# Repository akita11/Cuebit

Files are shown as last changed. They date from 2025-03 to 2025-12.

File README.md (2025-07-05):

# Cue:bit

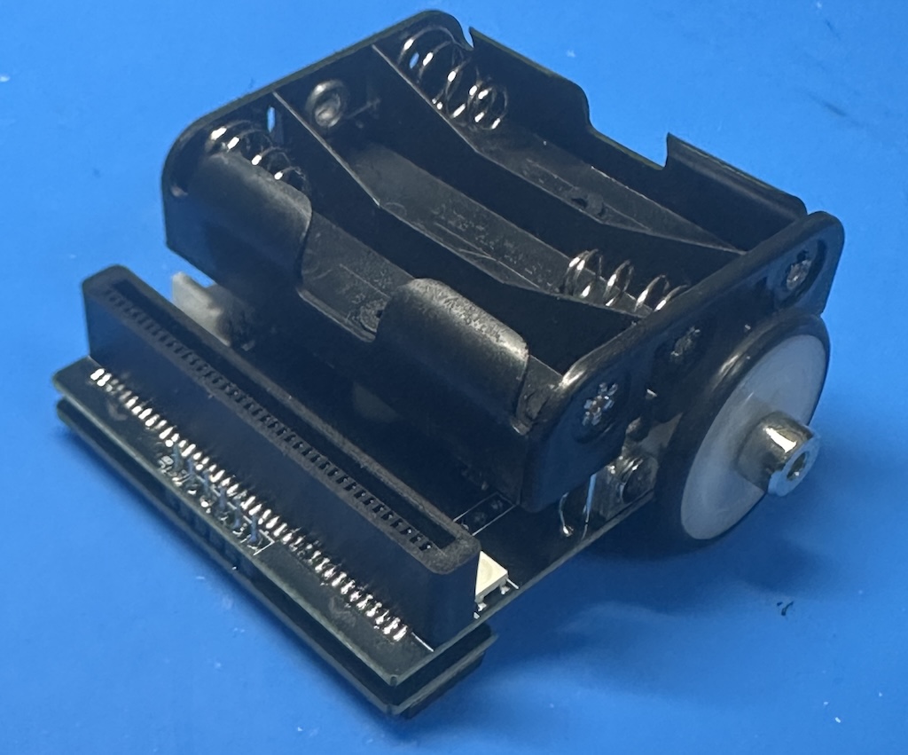
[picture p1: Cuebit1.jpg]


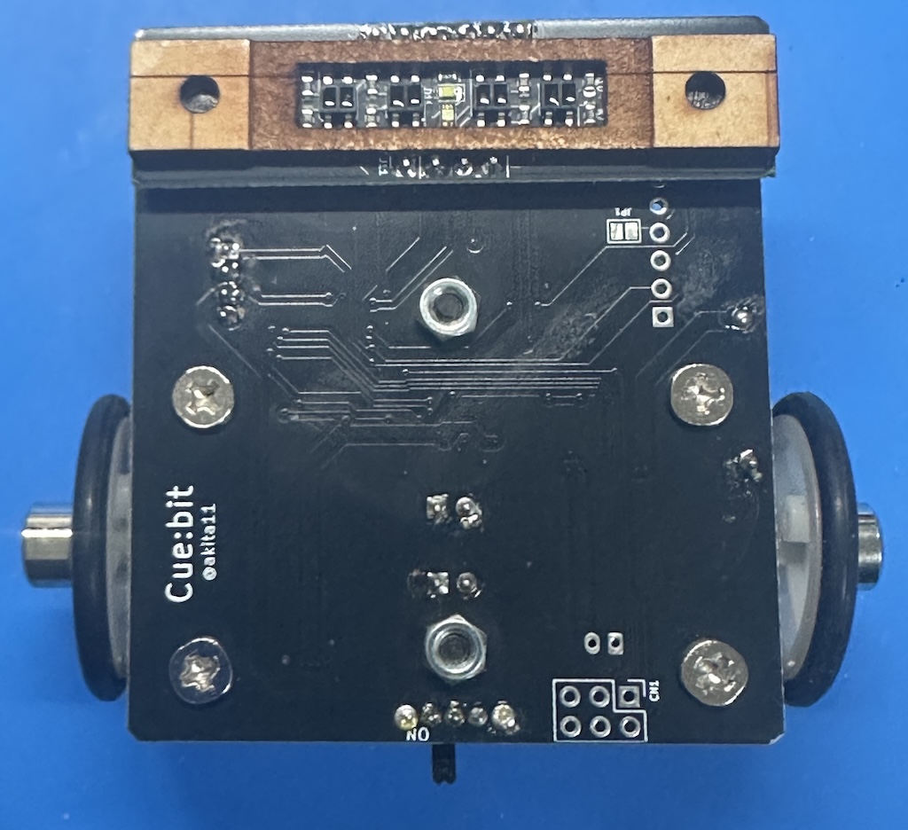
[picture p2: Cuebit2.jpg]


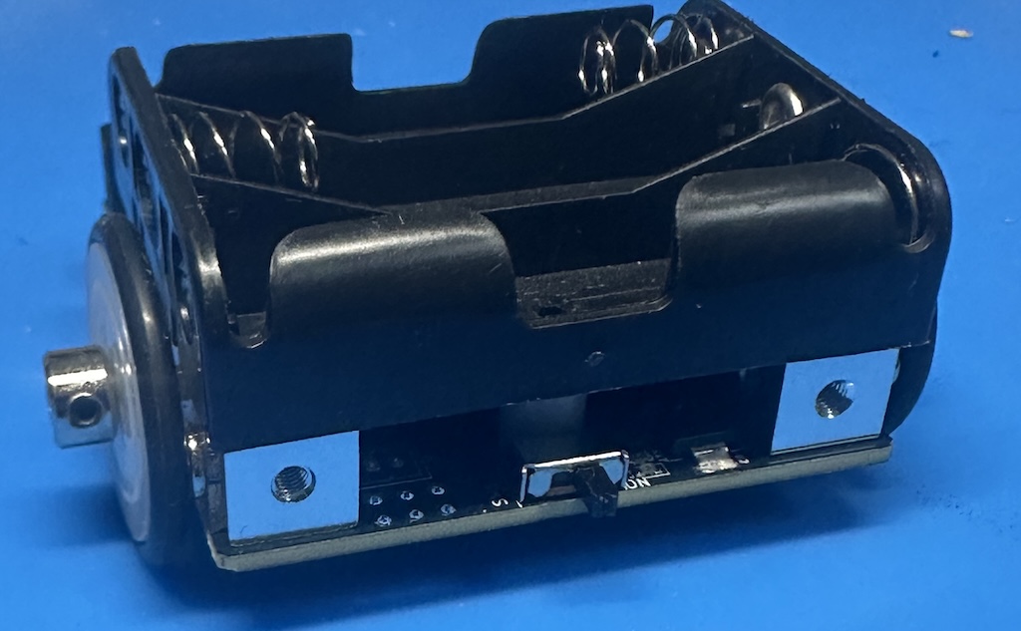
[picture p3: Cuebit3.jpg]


ライントレースと3色のカラーマーカでの動作制御ができるプログラミング教材ロボットカーです。micro:bitを装着して、micro:bitのカスタムブロックで動作制御することもできます。

[使い方・動作の例(YouTube動画)](https://youtu.be/czKjS_mCOlM)

## 使い方（ライントレースモード）

電源を入れると、ライントレースを開始します。また途中にカラーマーカーがあると、それに応じた動作をします。なおライン（黒）やカラーマーカを見失って0,5秒程度経過すると、自動的に停止します（本体LEDが黄色点灯）。ラインやマーカのあるところに移動させると、動作を再開します。

### カラーマーカーと動作の定義

赤・緑・黄の3色のマーカを3つ連続して配置されたところを通過すると、その色パターンに応じた動作を行います。色マーカは10mm程度の「丸ポチシール」（DAISOなどで売っているもの）や、同等の色を印刷したものを使います。(赤=R／緑=G／黄=Y）

- 緑-赤-黄 (GRY) : 速度を超ゆっくりに
- 赤-緑-黄 (RGY) : 速度をゆっくりに
- 赤-緑-赤 (RGR) : 速度を通常に
- 黄-緑-赤 (YGR) : 速度を速く
- 黄-赤-緑 (YRG) : 速度を超速く
- 黄-赤-黄 (YRY) : 一時停止（3秒程度）
- 緑-黄-赤 (GYR) : 次の交差点を左に90度曲がる
- 黄-緑-黄 (YGY) : 次の交差点を直進する
- 緑-黄-緑 (GYG) : 次の交差点を右に90度曲がる
- 赤-黄-赤 (RYR) : Uターンする
- 緑-赤-緑 (GRG) : バックする

## 使い方（micro:bitモード）

micro:bitのカスタムブロックを使ってCue:bitの動作を制御でききます。
[こちらの手順](https://docs.google.com/document/d/1bRiQpdVX2RdSoQZLEZQx14lWcuVc2Sd8CT0sPL3RYwU/)でMakeCode用カスタムブロックを追加し、micro:bitのプログラムを作成してmicro:bitに書き込みます。その後、そのmicro:bitをCue:bitに差し込んでCue:bitの電源をいれると、そのプログラム通りにCue:bitが動作します。

※モータの特性仕様上、左右の回転速度には差があり、以下のコマンドである程度は調整はできますが、完全に直進したり正確に指定距離だけ進む・回転することはできません。ご了承ください。

### 参考：技術的仕様

micro:bitからCue:bitへのコマンド（通信プロトコル:UART 9600bps N81）は以下です。以下の"NNN"は数値(10進数)で与えるコマンドパラメータです。また各コマンドは行末コード(0x0d or 0x0a)で終端します。なおCue:bitのGroveコネクタと本体後部の6ピンコネクタ用端子(FTDI-Basic用)も、micro:bitの通信端子と並列に接続されています。なお[「Groveケーブル-USBシリアル接続ケーブル」](https://www.switch-science.com/products/9460)を使うと、FTDI-Basicと本体Grove端子とを接続できます。なおソースコードはArduinoIDE等で書き込むことができます。（ターゲットはProMini(ATmega328P, 3.3V/8MHz)。新品ATmega328Pではこれ用のブートローダを書き込む必要あり）

- $ : micro:bit制御モードに開始
- \# : micro:bit制御モードを終了
- RNNN : NNN度回転（NNNが正=時計回り、負=反時計回り）（※実際の回転角度はモータ特性のばらつきなどから多少の誤差があります）
- B : 停止
- FNNN : NNN[cm]進む（※実際の移動距離はモータ特性のばらつきなどから多少の誤差があります）
- ZNNN : ジグザグ走行（およそNNN[cm]）
- SNNN : スケート走行（およそNNN[cm]）

以下はデバッグ用のコマンド

- P : パラメータの表示
- T : ライントレースモードを開始
- t : ライントレースモードを終了して停止
- D : デバッグ情報の表示を開始（Dに続けてr/g/y/wを書くと、色センサの値を各色の学習用のCSV形式で出力）
- d : デバッグ表示の表示を停止
- kNNN : ライントレース制御のKpパラメータ（float型）
- KNNN : ライントレース制御のKdパラメータ（float型）
- vNNN : 通常走行時の速度（float型。モータ駆動のPWM比として与えるため、値の範囲は0.0〜1.0）
- rNNN : 左右モータの速度調整（PWMデューティー比）（float型）（左モータのPWM比×r=右モータのPWM比として計算するため、v×rが1.0以下となること）
- fNNN : 1cm進むための時間[単位は10ms]（※実際の移動距離はモータ特性のばらつきなどから多少の誤差があります）
- gNNN : 10度回転するための時間[単位は10ms]（※実際の回転角度はモータ特性のばらつきなどから多少の誤差があります）
- ! : 各種パラメータをEEPROMに保存（起動時に読み込まれる）

## Author

Junichi Akita (@akita11) / akita@ifdl.jp

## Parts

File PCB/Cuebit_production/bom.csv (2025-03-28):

Designator | Footprint | Quantity | Value | LCSC Part #
C1, C2, C4, C5, C7 | C_0603_1608Metric | 5 | 0.1u | C14663
C3 | C_0603_1608Metric | 1 | 10u | C109454
D1 | LED_0603_1608Metric | 2 | LED(W) | C7371902
D2 |  |  | LED(G) | C165982
D3, D7 | LED_WS2812B_PLCC4_5.0x5.0mm_P3.2mm | 2 | WS2812B | C22461793
Q1 | SOT-23 | 1 | TR_NMOS_IRLML6344 | C20917
R10, R11, R15, R16, R5 | R_0603_1608Metric | 5 | 10k | C25804
R12, R13, R14, R7, R9 | R_0603_1608Metric | 5 | 470 | C2907172
R17 | R_0603_1608Metric | 1 | 1k | C21190
R18 | R_0603_1608Metric | 1 | 100 | C103204
R6, R8 | R_0603_1608Metric | 2 | 4.7k | C103656
U1 | TQFP-32_7x7mm_P0.8mm | 1 | ATmega328P-A | C14877
U2 | SOT-223-3_TabPin2 | 1 | AP1117-33 | C2763399
U3, U4 | SOT-23-6_L2.9-W1.6-P0.95-LS2.8-BL | 2 | AD116 | C2845121
U5, U6, U8, U9 | Everlight_ITR1201SR10AR | 4 | ITR8307-S17-TR8 | C81632
U7 | OPLGA-4 | 1 | SENSOR_VEML6040 | C78465
R1 | R_0603_1608Metric | 1 | 200k | C2907122
R2 | R_0603_1608Metric | 1 | 300k | C23024

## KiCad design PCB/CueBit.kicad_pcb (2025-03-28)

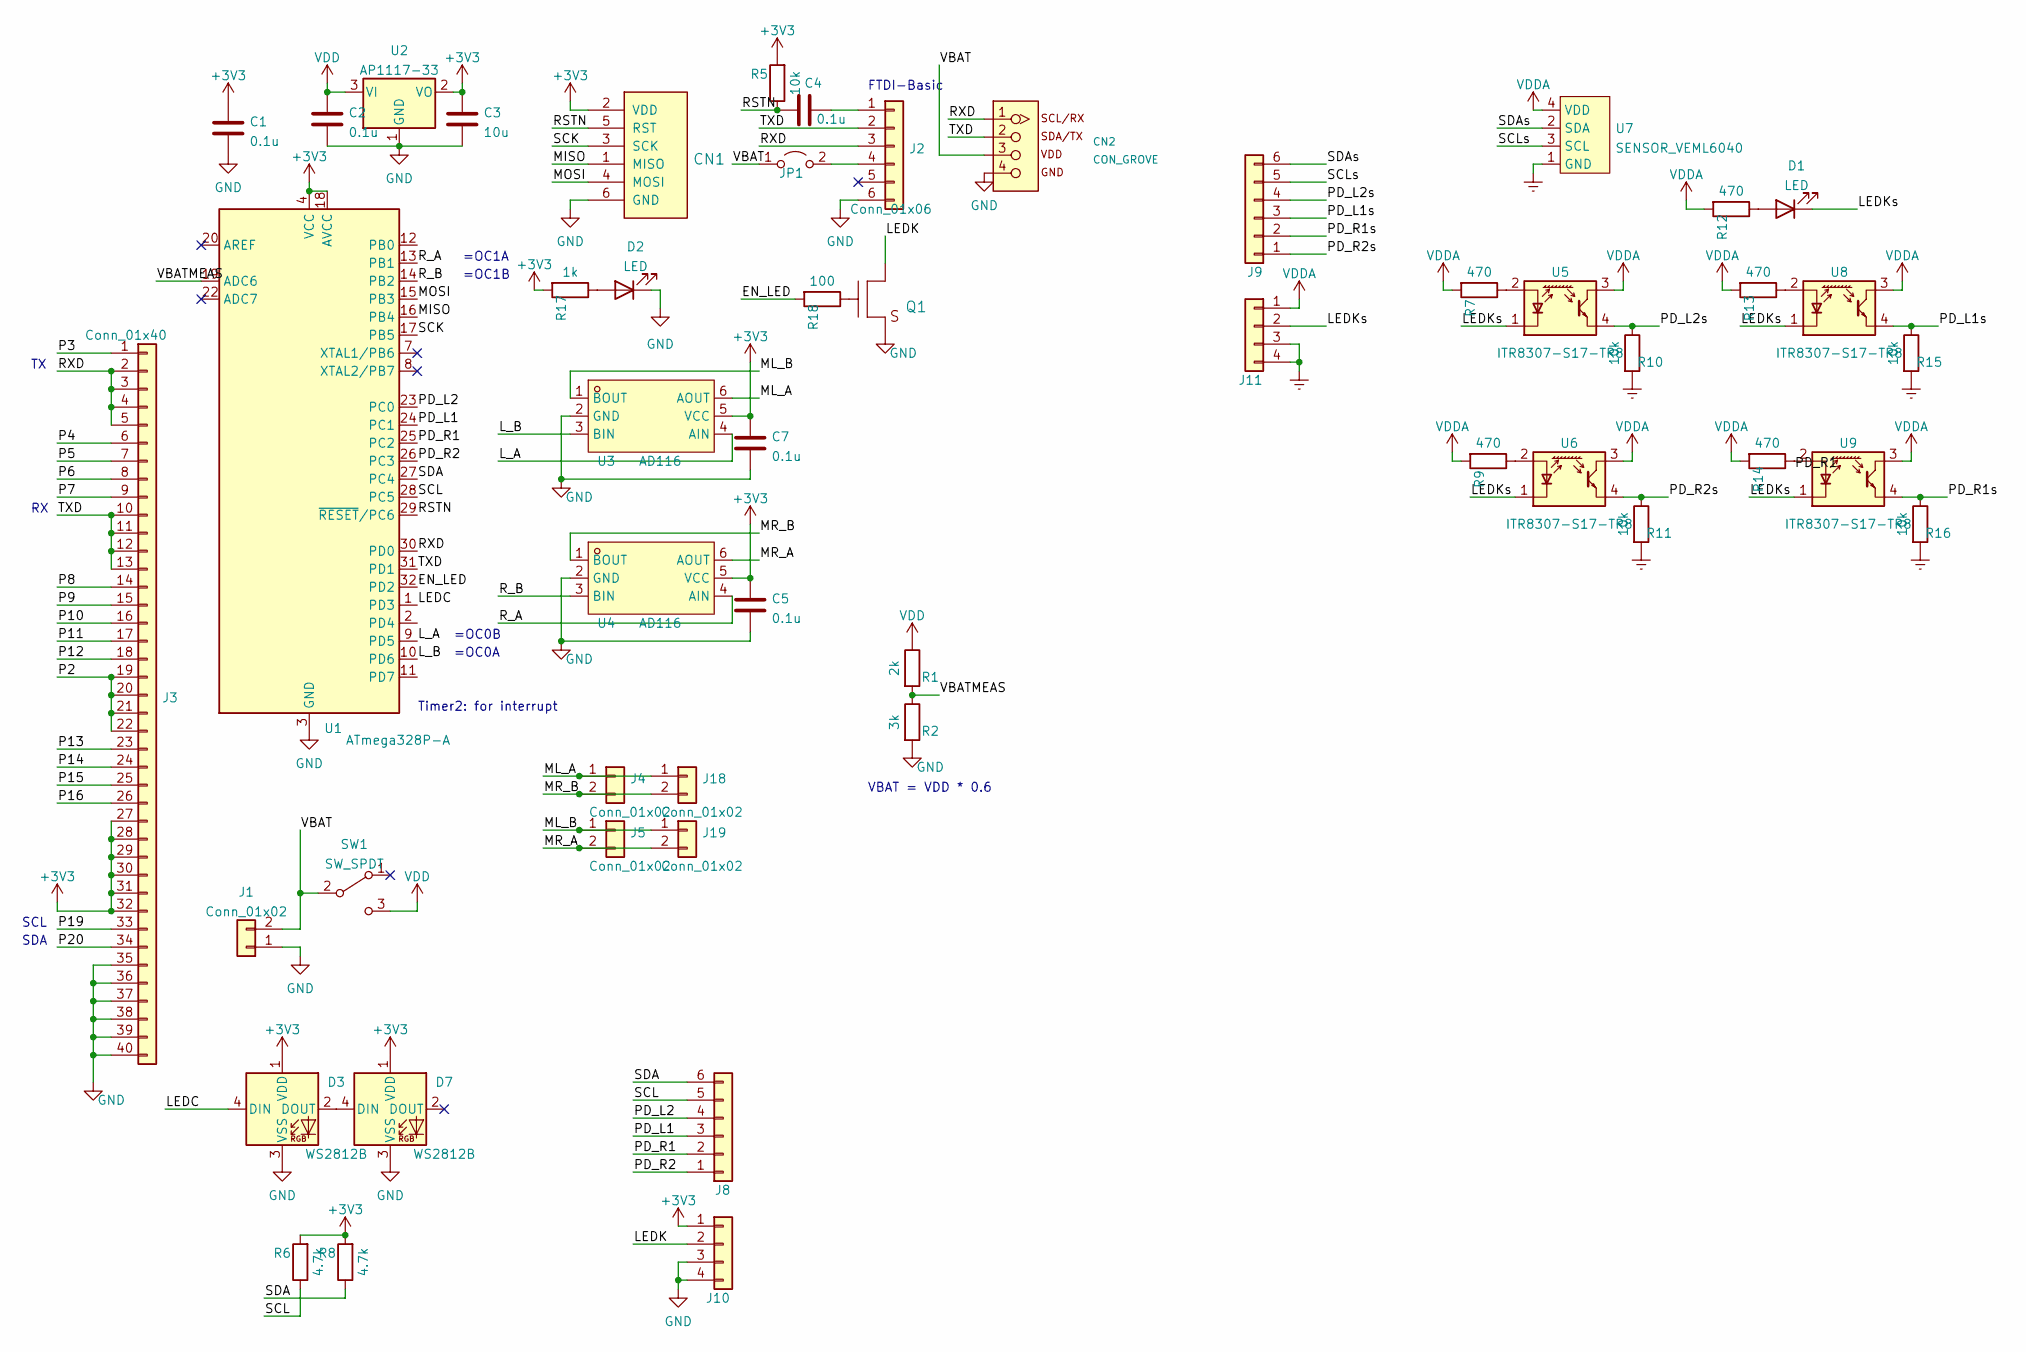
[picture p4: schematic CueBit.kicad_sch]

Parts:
C1, C2, C4, C5, C7: 0.1u; C_0603_1608Metric
C3: 10u; C_0603_1608Metric
CN1: CON_AVRISP; PinHeader_2x03_P2.54mm_Vertical
CN2: CON_GROVE; CON_GROVE_H_roundPad
D1, D2: LED; LED_0603_1608Metric
D3, D7: WS2812B; LED_WS2812B_PLCC4_5.0x5.0mm_P3.2mm
J1: Conn_01x02; JST_PH_B2B-PH-K_1x02_P2.00mm_Vertical
J2: Conn_01x06; PinSocket_1x06_P2.54mm_Vertical
J3: Conn_01x40; CON_microbit_cardedge_V_SMD
J4, J5: Conn_01x02; PinHeader_1x02_P2.54mm_Vertical
J8, J9: Conn_01x06; PinHeader_1x06_P2.54mm_Vertical
J10, J11: Conn_01x04; PinSocket_1x04_P2.54mm_Vertical
J18, J19: Conn_01x02; PinHeader_1x02_P2.54mm_Vertical_SMD_Pin1Right
JP1: Jumper_2_Open; SolderJumper-2_P1.3mm_Open_Pad1.0x1.5mm
Q1: TR_NMOS_IRLML6344; SOT-23
R1: 2k; R_0603_1608Metric; LCSC C2907022
R2: 3k; R_0603_1608Metric; LCSC C328357
R5, R10, R11, R15, R16: 10k; R_0603_1608Metric
R6, R8: 4.7k; R_0603_1608Metric
R7, R9, R12, R13, R14: 470; R_0603_1608Metric; LCSC C2907172
R17: 1k; R_0603_1608Metric
R18: 100; R_0603_1608Metric
SW1: SW_SPDT; SW_SK-12D11VG3
U1: ATmega328P-A; TQFP-32_7x7mm_P0.8mm; LCSC C14877
U2: AP1117-33; SOT-223-3_TabPin2; LCSC C2992570
U3, U4: AD116; SOT-23-6_L2.9-W1.6-P0.95-LS2.8-BL; LCSC Part C7463412
U5, U6, U8, U9: ITR8307-S17-TR8; Everlight_ITR1201SR10AR; LCSC C81632
U7: SENSOR_VEML6040; OPLGA-4; LCSC C78465

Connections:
+3V3: C1.1, C3.1, C5.1, C7.1, CN1.2 (VDD), D3.1 (VDD), D7.1 (VDD), J3.27, J3.28, J3.29, J3.30, J3.31, J3.32, J10.1, R5.2, R6.2, R8.2, R17.2, U1.4 (VCC), U1.6 (VCC), U1.18 (AVCC), U2.2 (VO), U3.5 (VCC), U4.5 (VCC)
/EN_LED: R18.2, U1.32 (PD2)
/LEDC: D3.4 (DIN), U1.1 (PD3)
/LEDK: J10.2, Q1.3 (D)
/LEDKs: D1.1 (K), J11.2, U5.1 (K), U6.1 (K), U8.1 (K), U9.1 (K)
/L_A: U1.9 (PD5), U3.4 (AIN)
/L_B: U1.10 (PD6), U3.3 (BIN)
/MISO: CN1.1 (MISO), U1.16 (PB4)
/ML_A: J4.1, J18.1, U3.6 (AOUT)
/ML_B: J5.1, J19.1, U3.1 (BOUT)
/MOSI: CN1.4 (MOSI), U1.15 (PB3)
/MR_A: J5.2, J19.2, U4.6 (AOUT)
/MR_B: J4.2, J18.2, U4.1 (BOUT)
/P2: J3.19, J3.20, J3.21, J3.22
/P3: J3.1
/P4: J3.6
/P5: J3.7
/P6: J3.8
/P7: J3.9
/P8: J3.14
/P9: J3.15
/P10: J3.16
/P11: J3.17
/P12: J3.18
/P13: J3.23
/P14: J3.24
/P15: J3.25
/P16: J3.26
/P19: J3.33
/P20: J3.34
/PD_L1: J8.3, U1.24 (PC1)
/PD_L1s: J9.3, R15.1, U8.4
/PD_L2: J8.4, U1.23 (PC0)
/PD_L2s: J9.4, R10.1, U5.4
/PD_R1: J8.2, U1.25 (PC2)
/PD_R1s: J9.2, R16.1, U9.4
/PD_R2: J8.1, U1.26 (PC3)
/PD_R2s: J9.1, R11.1, U6.4
/RSTN: C4.1, CN1.5 (RST), R5.1, U1.29 (~RESET/PC6)
/RXD: CN2.1, J2.3, J3.2, J3.3, J3.4, J3.5, U1.30 (PD0)
/R_A: U1.13 (PB1), U4.4 (AIN)
/R_B: U1.14 (PB2), U4.3 (BIN)
/SCK: CN1.3 (SCK), U1.17 (PB5)
/SCL: J8.5, R6.1, U1.28 (PC5)
/SCLs: J9.5, U7.3 (SCL)
/SDA: J8.6, R8.1, U1.27 (PC4)
/SDAs: J9.6, U7.2 (SDA)
/TXD: CN2.2, J2.2, J3.10, J3.11, J3.12, J3.13, U1.31 (PD1)
/VBAT: CN2.3, J1.2, JP1.1 (A), SW1.2 (B)
/VBATMEAS: R1.2, R2.1, U1.19 (ADC6)
Earth: J11.3, J11.4, R10.2, R11.2, R15.2, R16.2, U7.1 (GND)
GND: C1.2, C2.2, C3.2, C5.2, C7.2, CN1.6 (GND), CN2.4, D2.1 (K), D3.3 (VSS), D7.3 (VSS), J1.1, J2.6, J3.35, J3.36, J3.37, J3.38, J3.39, J3.40, J10.3, J10.4, Q1.2 (S), R2.2, U1.3 (GND), U1.5 (GND), U1.21 (GND), U2.1 (GND), U3.2 (GND), U4.2 (GND)
unnamed: C4.2, J2.1
unnamed: D1.2 (A), R12.1
unnamed: D2.2 (A), R17.1
unnamed: D3.2 (DOUT), D7.4 (DIN)
unnamed: J2.4, JP1.2 (B)
unnamed: Q1.1 (G), R18.1
unnamed: R7.1, U5.2 (A)
unnamed: R9.1, U6.2 (A)
unnamed: R13.1, U8.2 (A)
unnamed: R14.1, U9.2 (A)
VDD: C2.1, R1.1, SW1.3 (C), U2.3 (VI)
VDDA: J11.1, R7.2, R9.2, R12.2, R13.2, R14.2, U5.3, U6.3, U7.4 (VDD), U8.3, U9.3

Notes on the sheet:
SDA
VBAT = VDD * 0.6
Timer2: for interrupt
FTDI-Basic
=OC1A
=OC1B
=OC0B
=OC0A
SCL

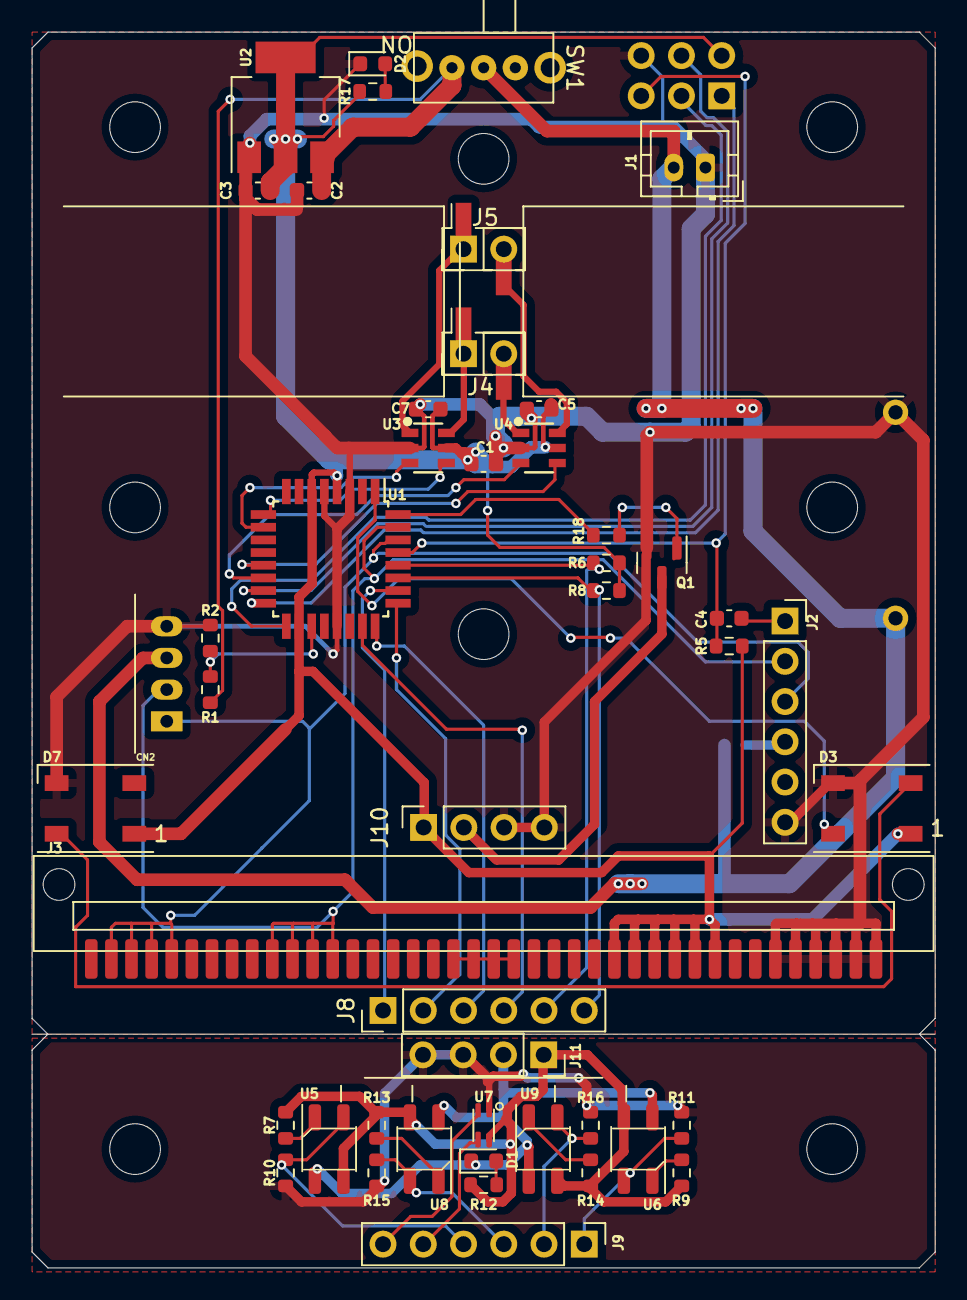
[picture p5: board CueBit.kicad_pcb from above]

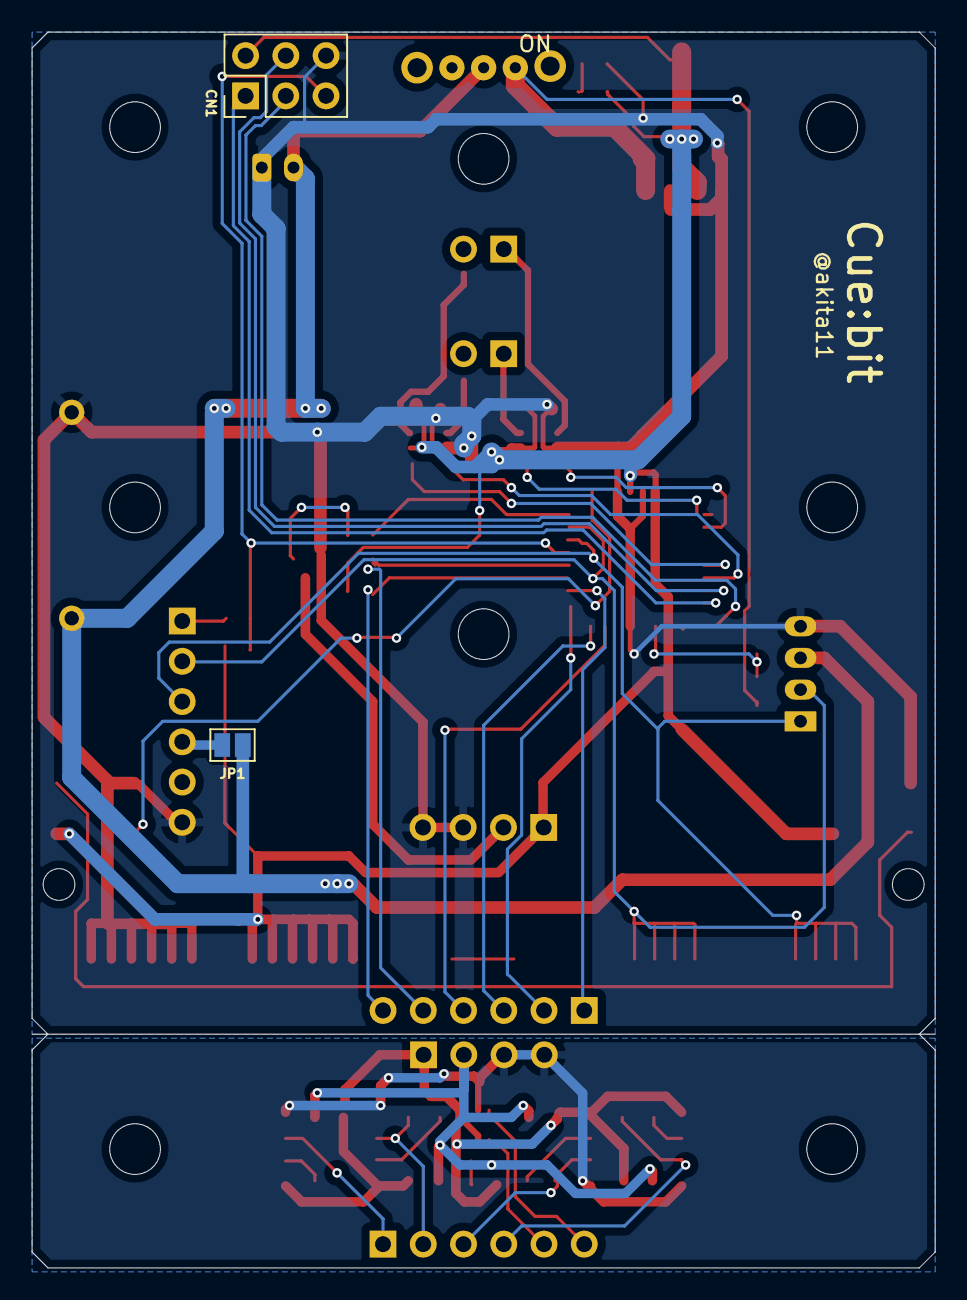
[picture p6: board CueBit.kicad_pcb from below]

Board: 2 copper layers, 57.0 x 78.0 mm, 51 parts (2 on the bottom side), 48 nets.

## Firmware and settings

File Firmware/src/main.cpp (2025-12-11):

#include <Arduino.h>
#include <MsTimer2.h>
#include "peripheral.h"
#include <EEPROM.h>

#define EEPROM_KP 0 // Kp*80
#define EEPROM_KD 1 // Kd*20
#define EEPROM_VN 2 // Vn*100
#define EEPROM_LR 3 // LRratio*100
#define EEPROM_TF 4 // tm1cm
#define EEPROM_TT 5 // tm10deg

// Motion Control Parameters
float Kp; // P gain for Line trace
float Kd; // D gain for Line trace
uint8_t tm1cm = 115; // [ms]
uint8_t tm10deg = 8; // [ms]
float vNormal, vVerySlow, vSlow, vFast, vVeryFast;

#define vNORMAL 0.3 // for turn and step go

float LRratio = 1.4;
float line_previous = 0;

//#define DELAY_AFTER_CROSS 50 // [x10ms]
#define DELAY_AFTER_CROSS 30 // [x10ms]

float vL = 0.0, vR = 0.0; // left/right motor speed (0.0 - 1.0)
uint8_t dirTrace = 0;
// motion types in micro:bit cmd mode
#define MOTION_NONE				0 
#define MOTION_FWD				1
#define MOTION_BWD				2
#define MOTION_TURN_LEFT	3
#define MOTION_TURN_RIGHT	4
#define MOTION_ZIGZAG			5
#define MOTION_SKATE			6

// color mark command (3=R / 4=G / 5=B)
#define COLOR_CMD_VERY_SLOW        "435" // GRB
#define COLOR_CMD_SLOW             "345" // RGB
#define COLOR_CMD_NORMAL           "343" // RGR
#define COLOR_CMD_FAST             "543" // BGR
#define COLOR_CMD_VERY_FAST        "534" // BRG
#define COLOR_CMD_PAUSE            "535" // BRB
#define COLOR_CMD_LEFT_AT_CROSS    "453" // GBR
#define COLOR_CMD_FORWARD_AT_CROSS "545" // BGB 
#define COLOR_CMD_RIGHT_AT_CROSS   "454" // GBG
#define COLOR_CMD_UTURN            "353" // RBR
#define COLOR_CMD_GO_BACK          "434" // GRG
// pending commands
//#define COLOR_CMD_JUMP_LEFT        ""
//#define COLOR_CMD_JUMP_FORWARD     ""
//#define COLOR_CMD_JUMP_RIGHT       ""
//#define COLOR_CMD_JUMP_HURRICANE   ""
//#define COLOR_CMD_ZIGZAG           ""
//#define COLOR_CMD_SPIN             ""

// flag for operation
uint8_t fMotion = MOTION_NONE; // currently operating motion
uint8_t fLineTrace = 1; // Line trace mode at power on
uint8_t fDebug = 0; // debug output of sensor data

uint8_t detectedColor;
uint16_t	 tm10ms = 0;
uint8_t fCross = 0; // "Cross point" detected

#define N_BUF 64 // Serial RX buffer size
char buf[N_BUF];
uint8_t pBuf = 0;

// Variables for color command in line trace mode 
uint8_t nColorCmd = 0;
#define MAX_COLOR_CMD 10
char ColorCmds[MAX_COLOR_CMD];
uint8_t pColorCmd = COLOR_WHITE;
uint8_t pColor = COLOR_WHITE;
uint8_t ColorCmd = COLOR_WHITE;
uint8_t nColorContinuous = 0;

uint8_t stateColorCmd = 0;
#define COLOR_CMD_ST_PAUSE             1
#define COLOR_CMD_ST_CROSS_TO_LEFT     4
#define COLOR_CMD_ST_CROSS_LEFT        3
#define COLOR_CMD_ST_CROSS_FORWARD     4
#define COLOR_CMD_ST_CROSS_TO_RIGHT    5
#define COLOR_CMD_ST_CROSS_RIGHT       6
#define COLOR_CMD_ST_UTURN             7
#define COLOR_CMD_ST_GOING_AFTER_CROSS 8
uint8_t cmdTurnAtCross = 0;

double leftDevi = 1.0, rightDevi = 1.0;
uint8_t tSkate = 0;
#define SKATE_CYCLE 100 // [x 10ms]

uint8_t stateZigzag = 0;
#define ZIGZAG_STEP 100 // [x 10ms] of half cycle
#define ZIGZAG_TURN 50 // [x 10ms] of turn time

uint8_t fLEDmsg = 0;
uint8_t stLEDmsg = 0;
uint8_t cntLEDmsg = 0;
uint8_t cntNoLine = 0;
uint8_t fNoLine = 0;
#define TIME_NOLINE 50 // [x10ms]

// every 10ms
void timerISR()
{
	if (tm10ms > 0) tm10ms--;
	if (fMotion == MOTION_SKATE){
		leftDevi = 1.0 + 0.3 * sin((double)tSkate / (double)SKATE_CYCLE * 2 * 3.14);
		rightDevi = 1.0 - 0.3 * sin((double)tSkate / (double)SKATE_CYCLE * 2 * 3.14);
		tSkate = (tSkate + 1) % SKATE_CYCLE;
	}
	if (fMotion == MOTION_ZIGZAG){
		stateZigzag = (stateZigzag + 1) % (ZIGZAG_STEP * 2);
	}
	if (stLEDmsg != LEDMSG_NONE){
		cntLEDmsg++;
		if (cntLEDmsg > 10){
			cntLEDmsg = 0;
			fLEDmsg = (fLEDmsg + 1) % 10;
			if (stLEDmsg == LEDMSG_LOW_BATTERY){
				if ((fLEDmsg % 2) == 1) setLED(20, 0, 0); // red
				else setLED(0, 0, 0);
			}
			else if (stLEDmsg == LEDMSG_LOST_LINE){
				if ((fLEDmsg % 2) == 1) setLED(20, 20, 0); // yellow
				else setLED(0, 0, 0);
			}
			else if (stLEDmsg == LEDMSG_MICROBIT){
				if (fLEDmsg > 5) setLED(10, 0, 10); // purple
				else setLED(0, 0, 0);
			}
		}
	}
	if (fNoLine == 1){
		if (cntNoLine < TIME_NOLINE) cntNoLine++;
	}
	else cntNoLine = 0;
}

void setSpeedParams()
{
	vVerySlow = vNormal * 0.5;
	vSlow = vNormal * 0.6;
	vFast = vNormal * 1.5;
	vVeryFast = vNormal * 2.0;
}

void setup() {
	Serial.begin(9600);
//	analogWrite(11, 128); while(1); // for OSC calib, 244.14Hz on MOSI

	if (EEPROM.read(EEPROM_KP) < 255) Kp = (float)EEPROM.read(EEPROM_KP) / 80.0;
	else Kp = 0.7;
	if (EEPROM.read(EEPROM_KD) < 255) Kd = (float)EEPROM.read(EEPROM_KD) / 20.0;
	else Kd = 5.0;
	if (EEPROM.read(EEPROM_VN) < 100) vNormal = (float)EEPROM.read(EEPROM_VN) / 100.0;
	else vNormal = 0.3;
	if (EEPROM.read(EEPROM_LR) < 255) LRratio = (float)EEPROM.read(EEPROM_LR) / 100.0;
	else LRratio = 1.0;
	if (EEPROM.read(EEPROM_TF) < 255) tm1cm = EEPROM.read(EEPROM_TF);
	else tm1cm = 90;
	if (EEPROM.read(EEPROM_TT) < 255) tm10deg = EEPROM.read(EEPROM_TT);
	else tm10deg = 5;

	setSpeedParams();

	Serial.print("Kp="); Serial.print(Kp); Serial.print(" Kd="); Serial.print(Kd); Serial.print(" Vn="); Serial.print(vNormal); Serial.print(" LR="); Serial.println(LRratio);
	init_peripheral();
	MsTimer2::set(10, timerISR); // every 10ms
	MsTimer2::start();
}

// ToDo: L&R motor calibration using straight move

int16_t getParam(char *s){
	if ((s[0] >= '0' && s[0] <= '9') || s[0] == '-' ) return(atoi(s));
	else return(0);
}

#define LOW_BATTERY_TH_HL 3.5 // [V], with LDO of Vdrop=0.2V
#define LOW_BATTERY_TH_LH 4.0 // [V], with LDO of Vdrop=0.2V
float sumBatteryVoltage = 0.0;
uint8_t nSumBatteryVolgate = 0;
#define N_SUM_BATTERY_VOLTAGE 50
float BatteryVoltage = 0.0;

float getBatteryVoltage()
{
	float v;
	v = analogRead(A6)  * (3.3 / 0.6) / 1023.0; // Vbat = VDD * 0.6
	return(v);	
}

uint8_t checkDebugging()
{
	if (fDebug == 0 || fDebug == 6) return(0);
	else return(1);
}

void loop() {
	sumBatteryVoltage += getBatteryVoltage();
	nSumBatteryVolgate++;
	if (nSumBatteryVolgate == N_SUM_BATTERY_VOLTAGE){
		BatteryVoltage = sumBatteryVoltage / N_SUM_BATTERY_VOLTAGE;
		sumBatteryVoltage = 0;
		nSumBatteryVolgate = 0;
		if (stLEDmsg != LEDMSG_LOW_BATTERY){
			if (BatteryVoltage <= LOW_BATTERY_TH_HL) stLEDmsg = LEDMSG_LOW_BATTERY;
		}
		else if (stLEDmsg == LEDMSG_LOW_BATTERY){
			if (BatteryVoltage >= LOW_BATTERY_TH_LH) stLEDmsg = LEDMSG_NONE;
		}
	}
	
	if (fLineTrace == 1){
		if (stateColorCmd == COLOR_CMD_ST_PAUSE){
			if (tm10ms > 0) setMotorSpeed(0, 0);
			else stateColorCmd = 0;
		}
		else if (stateColorCmd == COLOR_CMD_ST_UTURN){
			if (tm10ms > 0) setMotorSpeed(-vNORMAL, vNORMAL);
			else stateColorCmd = 0;
		}
		else if (cmdTurnAtCross == COLOR_CMD_ST_CROSS_LEFT || cmdTurnAtCross == COLOR_CMD_ST_CROSS_RIGHT){
			// tm10ms
			// - DELAY_AFTER_CROSS+tm10deg*9 - tm10deg*9 : go forward after cross
			// - tm10deg*9 - 0                           : turn left/right
//			Serial.print(cmdTurnAtCross); Serial.print(':'); Serial.println(tm10ms);
			if (tm10ms > tm10deg * 9) setMotorSpeed(vNORMAL, vNORMAL); // go forward after cross
			else if (tm10ms > 0){
				if (cmdTurnAtCross == COLOR_CMD_ST_CROSS_LEFT) fMotion = MOTION_TURN_LEFT;
				else fMotion = MOTION_TURN_RIGHT;
			}
		}

		if (fMotion == MOTION_TURN_RIGHT){
			fNoLine = 0; cntNoLine = 0;
			if (tm10ms > 0) setMotorSpeed(vNORMAL, -vNORMAL);
			else{
				stateColorCmd = 0;
				fMotion = MOTION_NONE;
			}
		}
		else if (fMotion == MOTION_TURN_LEFT){
			fNoLine = 0; cntNoLine = 0;
			if (tm10ms > 0) setMotorSpeed(-vNORMAL, vNORMAL);
			else{
				stateColorCmd = 0;
				fMotion = MOTION_NONE;
			}
		}
		else{
			// line trace mode
			SensorData sd;
			sd = readSensor(sd);
			detectedColor = sd.color;

			// differential value of lineValue
			float d_line = sd.line - line_previous;
			line_previous = sd.line;

			// color command detection	
#define COLOR_MARK_TH 10
			if (sd.color == pColor) nColorContinuous++;
			else{
//			if (nColorContinuous > COLOR_MARK_TH){
//				Serial.print(pColor); Serial.print(':'); Serial.println(nColorContinuous);
//			}
				nColorContinuous = 0;
			}
			pColor = sd.color;
			if (nColorContinuous > COLOR_MARK_TH){
				// color mark detected (spike noise removed)
				ColorCmd = sd.color;
				if (ColorCmd != pColorCmd){
					// color mark changed
					if (ColorCmd != COLOR_WHITE && ColorCmd != COLOR_BLACK){
						ColorCmds[nColorCmd] = '0' + ColorCmd;
						nColorCmd++;
						if (nColorCmd == MAX_COLOR_CMD){
							// color command buffer full, ignore buffer
							nColorCmd = 0;
						}
					}
					if ((ColorCmd == COLOR_BLACK || ColorCmd == COLOR_WHITE) && (pColorCmd != COLOR_BLACK && pColorCmd != COLOR_WHITE)){
						ColorCmds[nColorCmd] = '\0';
						// end of color command
						if (checkDebugging() == 0){
							Serial.print(nColorCmd); Serial.print('*'); Serial.println(ColorCmds);
						}
						if (nColorCmd >= 3){
							// execute motion
							if (strncmp(ColorCmds, COLOR_CMD_VERY_SLOW, 3) == 0){
							if (checkDebugging() == 0) Serial.println("CMD:veryslow");
							vNormal = vVerySlow;
						}
							if (strncmp(ColorCmds, COLOR_CMD_SLOW, 3) == 0){
							if (checkDebugging() == 0) Serial.println("CMD:slow");
							vNormal = vSlow;
						}
							if (strncmp(ColorCmds, COLOR_CMD_NORMAL, 3) == 0){
							if (checkDebugging() == 0) Serial.println("CMD:normal");
							vNormal = vNORMAL;
						}
							if (strncmp(ColorCmds, COLOR_CMD_FAST, 3) == 0){
							if (checkDebugging() == 0) Serial.println("CMD:fast");
							vNormal = vFast;
						}
							if (strncmp(ColorCmds, COLOR_CMD_VERY_FAST, 3) == 0){
							if (checkDebugging() == 0) Serial.println("CMD:veryfast");
							vNormal = vVeryFast;
						}
							if (strncmp(ColorCmds, COLOR_CMD_PAUSE, 3) == 0){
								if (checkDebugging() == 0) Serial.println("CMD:pause");
								tm10ms = 300; // pause time = 300ms
								stateColorCmd = COLOR_CMD_ST_PAUSE;
							}
							if (strncmp(ColorCmds, COLOR_CMD_LEFT_AT_CROSS, 3) == 0){
								if (checkDebugging() == 0) Serial.println("CMD:left at cross");
								tm10ms = 0;
								cmdTurnAtCross = COLOR_CMD_ST_CROSS_TO_LEFT;
							}
							if (strncmp(ColorCmds, COLOR_CMD_FORWARD_AT_CROSS, 3) == 0){
								if (checkDebugging() == 0) Serial.println("CMD:forward at cross");
								tm10ms = 0;
								cmdTurnAtCross = COLOR_CMD_ST_CROSS_FORWARD;
							}
							if (strncmp(ColorCmds, COLOR_CMD_RIGHT_AT_CROSS, 3) == 0){
								if (checkDebugging() == 0) Serial.println("CMD:right at cross");
								tm10ms = 0;
								cmdTurnAtCross = COLOR_CMD_ST_CROSS_TO_RIGHT;
							}
							if (strncmp(ColorCmds, COLOR_CMD_UTURN, 3) == 0){
								if (checkDebugging() == 0) Serial.println("CMD:u-turn");
								stateColorCmd = COLOR_CMD_ST_UTURN;
								tm10ms = tm10deg * 18; // turn 180deg
							}
							if (strncmp(ColorCmds, COLOR_CMD_GO_BACK, 3) == 0){
								if (checkDebugging() == 0) Serial.println("CMD:go back");
								dirTrace = 1 - dirTrace;
							}
						}
						nColorCmd = 0;
					}
					pColorCmd = ColorCmd;
				}
			}

			// P control
			if (sd.line < -5.0 || sd.color == COLOR_WHITE){
				// start count timer at marker/line lost
				fNoLine = 1;
				if (cntNoLine == TIME_NOLINE){
					// line lost for a while, stop
					vL = 0.0; vR = 0.0;
					if (stLEDmsg != LEDMSG_LOW_BATTERY) stLEDmsg = LEDMSG_LOST_LINE;
				}
			}
			else{
				fNoLine = 0;
				if (stLEDmsg != LEDMSG_LOW_BATTERY) stLEDmsg = LEDMSG_NONE;
				if (sd.line > 0.0){
					// line at right, turn right
					vL = vNormal;
					vR = vNormal - Kp * sd.line;
				}
				else if (sd.line < 0.0){
					// line at left, turn left
					vL = vNormal + Kp * sd.line;
					vR = vNormal;
				}
				else{
					vL = vNormal;
					vR = vNormal;
				}
				// D control
				vL += d_line * Kd;
				vR += d_line * Kd;
				if (vL > MAX_V) vL = MAX_V;
				else if (vL < MIN_V) vL = MIN_V;
				if (vR > MAX_V) vR = MAX_V;
				else if (vR < MIN_V) vR = MIN_V;
			}
			if (checkDebugging() == 0){
				if (dirTrace == 0) setMotorSpeed(vL, vR);
				else setMotorSpeed(-vR, -vL);
			}
			else setMotorSpeed(0, 0);

			// cross detection
			if (stateColorCmd != COLOR_CMD_ST_UTURN){
#define LINE_CROSS_TH 3.0
				if (sd.width > LINE_CROSS_TH){
					if (fCross == 0){
						fCross = 1;
						if (checkDebugging() == 0){
							Serial.print("cross "); Serial.println(cmdTurnAtCross);
						}
						if (cmdTurnAtCross == COLOR_CMD_ST_CROSS_TO_LEFT){
							// turn left at cross
							tm10ms = DELAY_AFTER_CROSS + tm10deg * 9;
							cmdTurnAtCross = COLOR_CMD_ST_CROSS_LEFT;
							if (checkDebugging() == 0) Serial.println("turn left at cross");
						}
						else if (cmdTurnAtCross == COLOR_CMD_ST_CROSS_TO_RIGHT){
							// turn right at cross
							tm10ms = DELAY_AFTER_CROSS + tm10deg * 9;
							cmdTurnAtCross = COLOR_CMD_ST_CROSS_RIGHT;
							if (checkDebugging() == 0) Serial.println("turn right at cross");
						}
						else if (cmdTurnAtCross == COLOR_CMD_ST_CROSS_FORWARD){
							if (checkDebugging() == 0) Serial.println("go forward at cross");
							cmdTurnAtCross = 0;
						}
					}
				}
				else fCross = 0;
			}
		}
	}
	else{
		// micro:bit command motion
		enableSensorLED(0);
		switch(fMotion){
			case MOTION_NONE : setMotorSpeed(0, 0); break;
			case MOTION_TURN_RIGHT:
				if (tm10ms > 0) setMotorSpeed(vNORMAL, -vNORMAL);
				else{ setMotorSpeed(0, 0); fMotion = MOTION_NONE;}
				break;
			case MOTION_TURN_LEFT:
				if (tm10ms > 0) setMotorSpeed(-vNORMAL, vNORMAL);
				else{ setMotorSpeed(0, 0); fMotion = MOTION_NONE;}
				break;
			case MOTION_FWD:
				if (tm10ms > 0) setMotorSpeed(vNORMAL, vNORMAL);
				else{ setMotorSpeed(0, 0); fMotion = MOTION_NONE;}
				break;
			case MOTION_BWD:
				if (tm10ms > 0) setMotorSpeed(-vNORMAL, -vNORMAL);
				else{ setMotorSpeed(0, 0); fMotion = MOTION_NONE;}
				break;
			case MOTION_ZIGZAG:
				if (tm10ms > 0){
					if (stateZigzag >= 0 && stateZigzag < ZIGZAG_TURN) setMotorSpeed(vNORMAL, -vNORMAL); // turn right
					else if (stateZigzag >= ZIGZAG_STEP && stateZigzag < ZIGZAG_STEP + ZIGZAG_TURN) setMotorSpeed(-vNORMAL, vNORMAL); // turn right
					else setMotorSpeed(vNORMAL, vNORMAL); // go straight
				}
				else {setMotorSpeed(0, 0); fMotion = MOTION_NONE;}
				break;
			case MOTION_SKATE:
//				Serial.print(tSkate); Serial.print(' '); Serial.print(vNORMAL*leftDevi); Serial.print(' '); Serial.println(vNORMAL*rightDevi);
				if (tm10ms > 0) setMotorSpeed(vNORMAL * leftDevi, vNORMAL * rightDevi);
				else {setMotorSpeed(0, 0); fMotion = MOTION_NONE;}
				break;
		}
	}

	int16_t param;
	while(Serial.available()){
		char c = Serial.read();
		if (c > 0){ // ignore non-ASCII characters
			if (c == '\r' || c == '\n'){
				buf[pBuf] = '\0';
				pBuf = 0;
				if (buf[0] == 'P'){
					Serial.print("Kp(k)="); Serial.print(Kp);
					Serial.print(" Kd(K)="); Serial.print(Kd); 
					Serial.print(" V(v)="); Serial.print(vNormal); 
					Serial.print(" LRr(r)="); Serial.print(LRratio);
					Serial.print(" tm1cm(f)="); Serial.print(tm1cm); 
					Serial.print(" tm10deg(g)="); Serial.println(tm10deg);
				}
				if (buf[0] == 'T') {fLineTrace = 1; pColorCmd = COLOR_WHITE; nColorCmd = 0; }
				if (buf[0] == 't') {fLineTrace = 0; setMotorSpeed(0, 0); }
				if (buf[0] == 'D'){
					 if (buf[1] == 'k') fDebug = 2;
					 else if (buf[1] == 'r') fDebug = 3;
					 else if (buf[1] == 'g') fDebug = 4;
					 else if (buf[1] == 'y') fDebug = 5;
					 else if (buf[1] == 'w') fDebug = 1;
					 else fDebug = 6;
				}
				if (buf[0] == 'd') fDebug = 0;
				if (buf[0] == 'k'){ Kp = atof(&buf[1]); Serial.println(Kp); }
				if (buf[0] == 'K'){ Kd = atof(&buf[1]); Serial.println(Kd); }
				if (buf[0] == 'r'){ LRratio = atof(&buf[1]); Serial.println(LRratio); }
				if (buf[0] == 'v'){ vNormal = atof(&buf[1]); Serial.println(vNormal); setSpeedParams(); }	
				if (buf[0] == 'f'){ tm1cm = atoi(&buf[1]); Serial.println(tm1cm); }
				if (buf[0] == 'g'){ tm10deg = atoi(&buf[1]); Serial.println(tm10deg); }
				if (buf[0] == '!'){
					EEPROM.write(EEPROM_KP, (uint8_t)(Kp * 80));
					EEPROM.write(EEPROM_KD, (uint8_t)(Kd * 20));
					EEPROM.write(EEPROM_VN, (uint8_t)(vNormal * 100));
					EEPROM.write(EEPROM_LR, (uint8_t)(LRratio * 100));
					EEPROM.write(EEPROM_TF, tm1cm);
					EEPROM.write(EEPROM_TT, tm10deg);
					Serial.println("parameters saved.");
				}
				// micro:bit command
				if (buf[0] == '$'){
					Serial.println("enter micro:bit command mode");
					fLineTrace = 0;
					setMotorSpeed(0, 0);
					stLEDmsg = LEDMSG_MICROBIT;
				}
				if (buf[0] == '#'){
					Serial.println("exit micro:bit command mode");
					fLineTrace = 1;
					stLEDmsg = LEDMSG_NONE;
				}
				if (buf[0] == 'R'){
					// Rxx turn right(+) or left(-) xx degree
					fLineTrace = 0;
					param = getParam(buf+1);
					if (param >0){
						fMotion = MOTION_TURN_RIGHT;
						tm10ms = tm10deg * param / 10;
						Serial.println(tm10ms);
					}
					else{
						fMotion = MOTION_TURN_LEFT;
						tm10ms = tm10deg * (-param) / 10;
					}
				}
				if (buf[0] == 'B'){
					// B stop
					fMotion = MOTION_NONE;
				}
				if (buf[0] == 'F'){
					// Fxx go straight xxcm
					param = getParam(buf+1);
					if (param > 0){
						fMotion = MOTION_FWD;
						tm10ms = tm1cm * param / 10;
					}
					else{
						fMotion = MOTION_BWD;
						tm10ms = tm1cm * (-param) / 10;
					}
				}
				if (buf[0] == 'Z'){
					// Zxx zig-zag xxcm
					param = getParam(buf+1);
					fMotion = MOTION_ZIGZAG;
					stateZigzag = 0;
					tm10ms = param * 20; // tentative
				}
				if (buf[0] == 'S'){
					// Sxx skate xxcm
					param = getParam(buf+1);
					fMotion = MOTION_SKATE;
					tSkate = 0;
					tm10ms = param * 20; // tentative
				}
			}
			else{ buf[pBuf++] = c; if (pBuf == N_BUF) pBuf = 0; }
		}
	}
}

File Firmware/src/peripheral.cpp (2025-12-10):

#include <Arduino.h>
#include "Wire.h"
#include "veml6040.h"
#include <Adafruit_NeoPixel.h>

#include "peripheral.h"

// https://github.com/thewknd/VEML6040/
VEML6040 RGBWSensor;

#define R_B    5 // PD5
#define R_A    6 // PD6
#define L_A    9 // PB1
#define L_B    10 // PB2
#define LEDC   3 // for WS2812
#define LED_EN 2 // PD2
#define PD_R2  A3
#define PD_R1  A2
#define PD_L1  A1
#define PD_L2  A0

// for wide sensor
#define BLACK_PD_R2 36
#define WHITE_PD_R2 360
#define BLACK_PD_R1 42
#define WHITE_PD_R1 342
#define BLACK_PD_L1 45
#define WHITE_PD_L1 400
#define BLACK_PD_L2 35
#define WHITE_PD_L2 350
#define BLACK_COLOR 11000
#define WHITE_COLOR 20000

#define MAX_PWM_L 255
#define MAX_PWM_R 255

Adafruit_NeoPixel pixel(2, LEDC, NEO_GRB + NEO_KHZ800);

void init_peripheral()
{
  pixel.begin(); pixel.clear();
	pinMode(LED_EN, OUTPUT);
	setLED(20, 0, 0);
	setMotorSpeed(0.0, 0.0);
	enableSensorLED(0);
  Wire.begin(); 
	RGBWSensor.setConfiguration(VEML6040_IT_40MS + VEML6040_AF_AUTO + VEML6040_SD_ENABLE);
  if(!RGBWSensor.begin()) {
    Serial.println("VEML6040 init error");
    while(1){ setLED(20, 0, 0); delay(100); setLED(0, 0, 0); delay(100); }
  }
}

void enableSensorLED(uint8_t f)
{
	if (f == 1) digitalWrite(LED_EN, HIGH);
	else digitalWrite(LED_EN, LOW);
}

uint16_t convMotorPWM(uint8_t max_pwm, float v){
	if (v > 1.0) return(max_pwm);
	else return((uint16_t)(max_pwm * v));
}

// vL/vR : -1 - +1 / +=FWD, -=BWD
void setMotorSpeed(float vL, float vR)
{
	if (vL > 0){
		analogWrite(L_A, convMotorPWM(MAX_PWM_L, vL));	analogWrite(L_B, 0);
	}
	else{
		analogWrite(L_A, 0); analogWrite(L_B, -convMotorPWM(MAX_PWM_L, vL));
	}
	if (vR > 0){
		analogWrite(R_A, convMotorPWM(MAX_PWM_R, vR * LRratio));	analogWrite(R_B, 0);
	}
	else{
		analogWrite(R_A, 0); analogWrite(R_B, -convMotorPWM(MAX_PWM_R, vR * LRratio));
	}
}

void setLED(uint8_t r, uint8_t g, uint8_t b)
{
	pixel.setPixelColor(0,  pixel.Color(r, g, b)); pixel.setPixelColor(1,  pixel.Color(r, g, b)); pixel.show();
}

uint8_t classify(float R, float G, float B, float W) {
	/*
	float weights[5][5] = {
		{-0.215193,  0.158631,  0.447248,  0.000700, -24.586008},
		{-0.478091, -0.265669,  0.986931, -0.001539,  21.651707},
		{ 0.355452, -0.928157, -0.255726,  0.000547,  32.428762},
		{-0.102398,  0.391205, -0.465644, -0.000426,  10.497819},
		{ 0.440230,  0.643990, -0.712809,  0.000718, -39.992280}
	};
	*/
	// data in 251211
	float weights[5][5] = {
	  {-0.511273, 0.538672, 0.358886, 0.000558, -26.676748},
  	{-0.172642, -0.442766, 0.599960, -0.001610, 35.171817},
  	{0.912427, -0.697076, -0.323679, 0.000352, -1.350221},
  	{-0.687868, 0.318697, -0.092341, 0.000292, 19.035786},
  	{0.459356, 0.282473, -0.542826, 0.000408, -26.180634}
	};
	float input[4] = {R, G, B, W};
	float scores[5];

	for (int c = 0; c < 5; c++) {
		scores[c] = weights[c][4]; // bias
		for (int i = 0; i < 4; i++) {
			scores[c] += input[i] * weights[c][i];
		}
	}

	int maxIndex = 0;
	for (int c = 1; c < 5; c++) {
		if (scores[c] > scores[maxIndex]) {
			maxIndex = c;
		}
	}

	if (maxIndex == 0) return(COLOR_WHITE);
	else if (maxIndex == 1) return(COLOR_BLACK);
	else if (maxIndex == 2) return(COLOR_RED);
	else if (maxIndex == 3) return(COLOR_GREEN);
	else return(COLOR_BLUE);
}

// BLACK(1.0) - WHITE(0.0)
float lineValue(uint16_t val, uint16_t vBlack, uint16_t vWhite){
	float v;
	if (val < vBlack) v = 1.0;
	else if (val > vWhite) v = 0.0;
	else v = (float)(vWhite - val) / (float)(vWhite - vBlack);
	return(v);
}

SensorData readSensor(SensorData sd)
{
	// return: L2:L1:C:R1:R2:{COLOR[2:0]} (1=line detected)
	uint8_t sensorInfo = COLOR_NONE;
	uint16_t sensorR, sensorG, sensorB, sensorW;

	enableSensorLED(1);
//	delay(2);

	float s = 0.0;
	float v;
	sd.line = 0.0;
	v = lineValue(analogRead(PD_L2), BLACK_PD_L2, WHITE_PD_L2); sd.line += v * (-2); s += v;
	v = lineValue(analogRead(PD_L1), BLACK_PD_L1, WHITE_PD_L1); sd.line += v * (-1); s += v;
	v = lineValue(analogRead(PD_R1), BLACK_PD_R1, WHITE_PD_R1); sd.line += v * (+1); s += v;
	v = lineValue(analogRead(PD_R2), BLACK_PD_R2, WHITE_PD_R2); sd.line += v * (+2); s += v;

	sensorR = RGBWSensor.getRed();
	sensorG = RGBWSensor.getGreen();
	sensorB = RGBWSensor.getBlue();
	sensorW = RGBWSensor.getWhite();
//	enableSensorLED(0);

	// normalize
	float sensorRf, sensorGf, sensorBf;
	sensorRf = (float)sensorR / (float)sensorW * 100.0;
	sensorGf = (float)sensorG / (float)sensorW * 100.0;
	sensorBf = (float)sensorB / (float)sensorW * 100.0;

/*
	if (sensorW > WHITE_COLOR) sensorInfo = COLOR_WHITE;
	else sensorInfo = classify(sensorRf, sensorGf, sensorBf, sensorW);
*/
	sensorInfo = classify(sensorRf, sensorGf, sensorBf, sensorW); // model including W 
	sd.color = sensorInfo;
	if (stLEDmsg == LEDMSG_NONE){
		if (sensorInfo == COLOR_BLACK) setLED(0, 0, 0);
		else if (sensorInfo == COLOR_RED) setLED(10, 0, 0);
		else if (sensorInfo == COLOR_GREEN) setLED(0, 10, 0);
//		else if (sensorInfo == COLOR_BLUE) setLED(0, 0, 10); // blue (old)
		else if (sensorInfo == COLOR_BLUE) setLED(6, 6, 0); // yellow
		else if (sensorInfo == COLOR_WHITE) setLED(10, 10, 10);
	}
	
	if (sensorInfo != COLOR_WHITE) s += lineValue(sensorW, BLACK_COLOR, WHITE_COLOR);	
//	if (s == 0.0) sd.line = -10.0;
	if (s <  0.3) sd.line = -10.0;
	else sd.line = sd.line / s;
	sd.width = s;
	if (fDebug > 0){
	 	Serial.print(sensorRf); Serial.print(",");
	 	Serial.print(sensorGf); Serial.print(",");
	 	Serial.print(sensorBf); Serial.print(",");
	 	Serial.print(sensorW); Serial.print(",");
		if (fDebug == 6){
	 		Serial.print("|,");
		 	Serial.print(analogRead(PD_R2)); Serial.print(',');
		 	Serial.print(analogRead(PD_R1)); Serial.print(',');
	 		Serial.print(analogRead(PD_L1)); Serial.print(',');
	 		Serial.print(analogRead(PD_L2)); Serial.print(",|,");
			Serial.print(lineValue(analogRead(PD_R2), BLACK_PD_R2, WHITE_PD_R2)); Serial.print(',');
			Serial.print(lineValue(analogRead(PD_R1), BLACK_PD_R1, WHITE_PD_R1)); Serial.print(',');
			Serial.print(lineValue(analogRead(PD_L1), BLACK_PD_L1, WHITE_PD_L1)); Serial.print(',');
			Serial.print(lineValue(analogRead(PD_L2), BLACK_PD_L2, WHITE_PD_L2)); Serial.print(',');
			if (sensorInfo != COLOR_WHITE) Serial.print(lineValue(sensorW, BLACK_COLOR, WHITE_COLOR));
			Serial.print(",|,"); Serial.print(sd.line);
			Serial.print(','); Serial.print(sd.width);
			Serial.print('/'); Serial.print(sd.color);
//			Serial.print('|'); Serial.print(vL); Serial.print(','); Serial.println(vR);
			Serial.print(','); Serial.print(BatteryVoltage);
			Serial.println("");
		}
		else if (fDebug >= 1 && fDebug <= 5) Serial.println(fDebug); // with color label
	}
	return(sd);
}

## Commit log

2024-07-28 functions for motors & sensors
2024-08-02 sensor calibration
2024-08-02 motor control
2024-08-27 for DC motor
2024-09-29 tentative line trace
2024-10-08 analog line trace
2024-10-29 tentative UART commands
2024-11-21 refactoring & timer ISR motion control
2024-11-22 enable sensor LED_EN as output
2024-12-16 param for wide sensor board
2024-12-17 color sensor black detection
2025-03-07 low battery detection
2025-04-09 LED blink debug
2025-12-11 add color_train_eval.py, stop motors during color logging
